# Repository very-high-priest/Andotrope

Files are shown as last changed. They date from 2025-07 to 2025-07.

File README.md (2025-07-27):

# Andotrope
afbeelding



Open Source andotrope I made, for anyone that wants to build their own andotrope.
Credit to the idea of an andotrope goes to Mike Ando https://www.riumplus.com/gehns-holographic-imager-andotrope/
I came up with the method of creating the see through effect.

This is just a prototype and certain things don't work properly yet, please read the issues.

We use a rp2040 zero as the main microcontroller.

Here's a link to the specific screens i bought: 
https://nl.aliexpress.com/item/1005004662221931.html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

Here's the link for the specific battery I bought:
https://www.amazon.com.be/-/nl/Lithium-polymeer-batterij-oplaadbare-connector/dp/B09DPP44C4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

Here's a link for the specific motor I bought:
https://nl.aliexpress.com/item/4001118243931.html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 

Here's a link for the specific magnets I bought:
https://www.digikey.be/nl/products/detail/radial-magnets-inc/8996/5126078

Here's a link for the specific power connector I bought for the motor:
https://www.digikey.be/nl/products/detail/tensility-international-corp/54-00287/16649080 

The powerbrick isn't for sale anymore so you'll have to buy your own 6V barrel connector powerbrick.

Here's the link for the polarised film I used: 
https://nl.aliexpress.com/item/1005006054349865.html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 

Unfortunately the screens themselves are polarised at a 45° angle so you'll have to add another polarisation filter on top if it polarising it horizontally or vertically so the wrap around filter doesn't block the light coming from the filter at the opposite side of the screen holder but only blocks light from the screen itself.

here's the heat inserts I used:
https://nl.aliexpress.com/item/1005003582355741.html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

Here's the screws I used for the heat inserts:
https://nl.aliexpress.com/item/1005005070119421.html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 

I sourced the powerswitch from old christmas lights and soldered it in between the batteries power line. 

The rest of the components you should be able to source from the bill of materials of the scematic.

Here's some more important tips:

Do not solder the mosfet to the bord but rather bridge the source and drain.
I myself glued the screens to the screen holder using double sided tape.
The polarised film has a protective film on both sides that needs to be removed, be carefull because one side of the film is very sticky and should be oriented inwards. This sticky side does help with sticking it to the screens but not to the outside of the screen holder. I used zip ties for that.

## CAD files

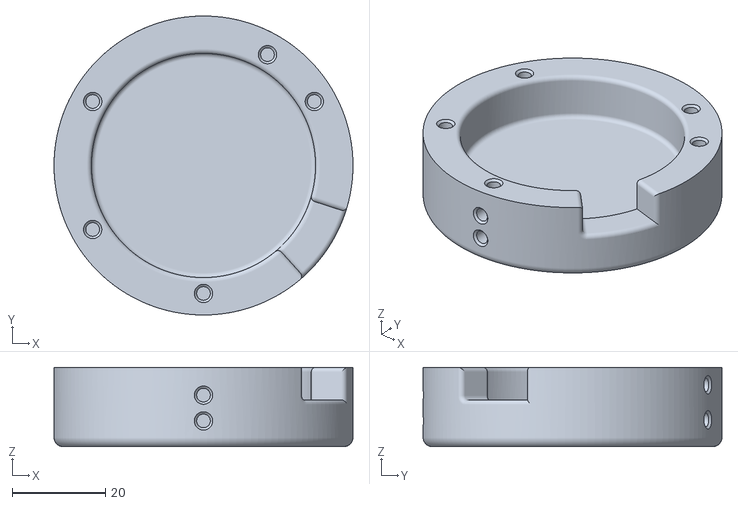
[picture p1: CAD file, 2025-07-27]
3d print files/PCB housing.stl
64.0 x 64.0 x 17.0

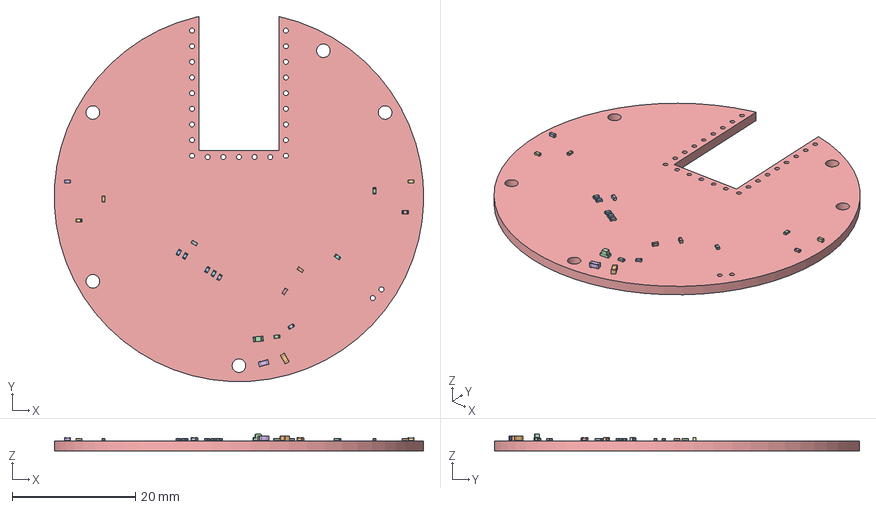
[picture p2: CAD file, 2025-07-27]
FreeCad design files/PCB.FCStd
60.0 x 59.3 x 2.75 mm
C_0402_1005Metric
C_0603_1608Metric
R_0402_1005Metric
LED_0603_1608Metric
R_0402_1005Metric002
C_0603_1608Metric002
C_0402_1005Metric002
R_0402_1005Metric004
R_0402_1005Metric006
R_0402_1005Metric008
R_0402_1005Metric010
R_0402_1005Metric012
C_0402_1005Metric004
C_0402_1005Metric006
R_0402_1005Metric014
R_0402_1005Metric016
R_0402_1005Metric018
C_0402_1005Metric008
R_0402_1005Metric020
R_0402_1005Metric022
abdotrope_PCB

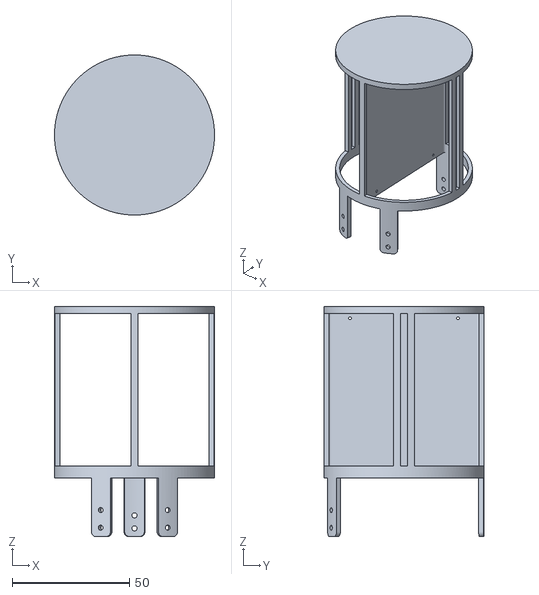
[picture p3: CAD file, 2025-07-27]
3d print files/screen housing.stl
68.2 x 68.2 x 98.0

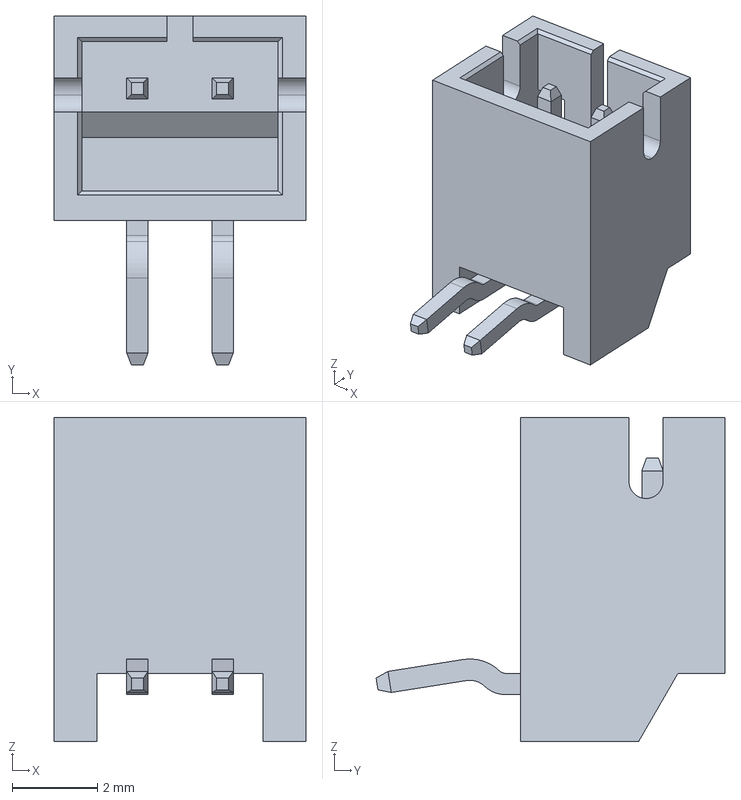
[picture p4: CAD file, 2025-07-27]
FreeCad design files/power connector.FCStd
5.90 x 8.18 x 7.60 mm

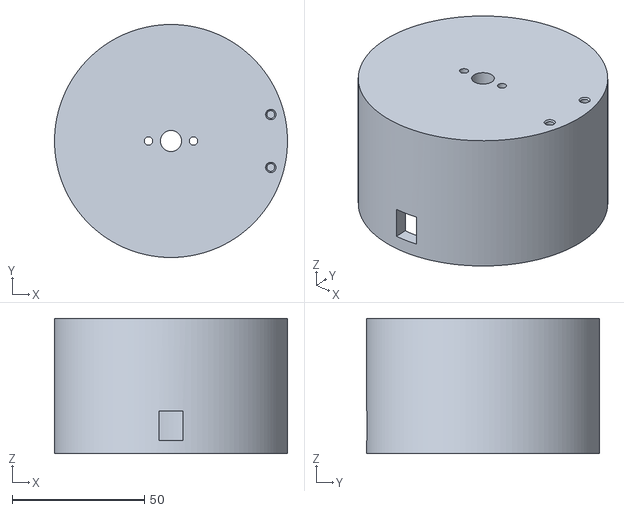
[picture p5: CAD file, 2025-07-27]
3d print files/motor holder.stl
88.0 x 88.0 x 51.0

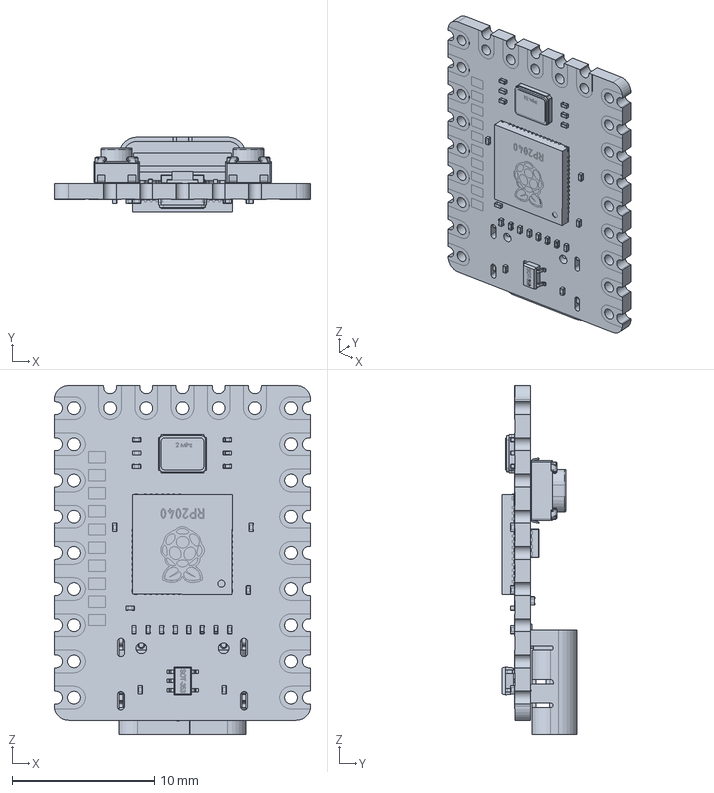
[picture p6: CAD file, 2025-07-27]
FreeCad design files/RP2040-ZERO.FCStd
18.0 x 5.26 x 24.5 mm

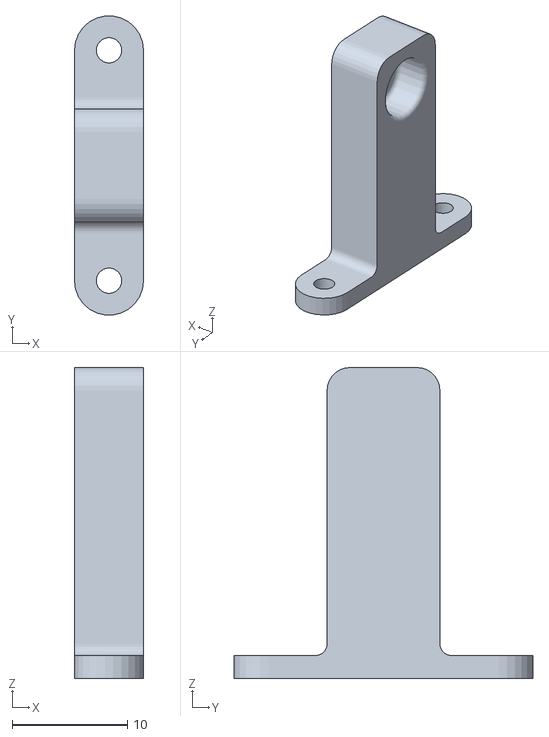
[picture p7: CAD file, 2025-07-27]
3d print files/magnet holder.stl
6.00 x 26.0 x 27.0

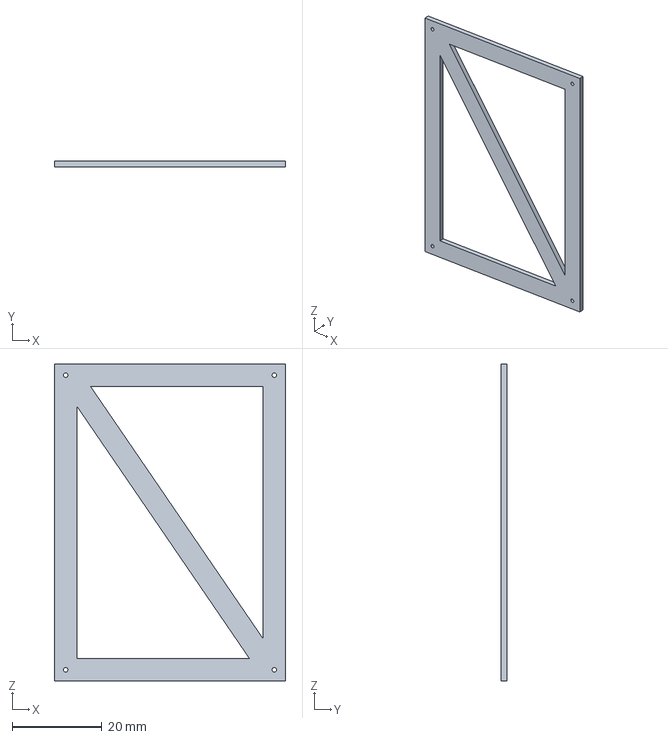
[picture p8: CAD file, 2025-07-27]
FreeCad design files/screen holder.FCStd
51.5 x 1.35 x 70.6 mm

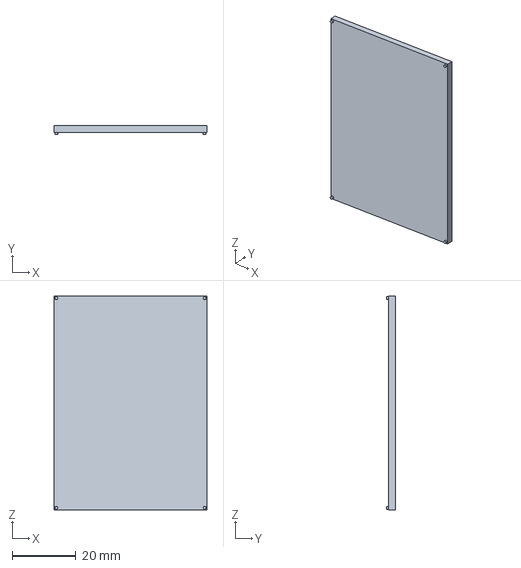
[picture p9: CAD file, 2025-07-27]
FreeCad design files/screen.FCStd
47.8 x 2.78 x 67.0 mm

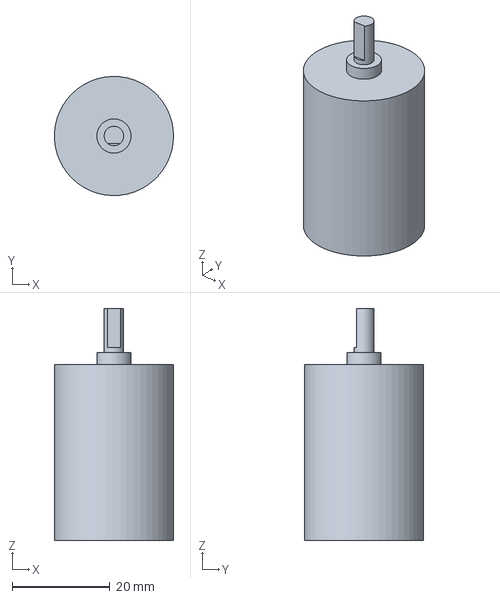
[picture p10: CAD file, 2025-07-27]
FreeCad design files/motor.FCStd
24.4 x 24.4 x 47.5 mm

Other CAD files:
FreeCad design files/spin_assembly.FCStd
FreeCad design files/screen assembly.FCStd
FreeCad design files/andotrope assembly.FCStd
FreeCad design files/blinds.FCStd
FreeCad design files/pcb Housing.FCStd
FreeCad design files/parameter.FCStd
FreeCad design files/motor housing.FCStd

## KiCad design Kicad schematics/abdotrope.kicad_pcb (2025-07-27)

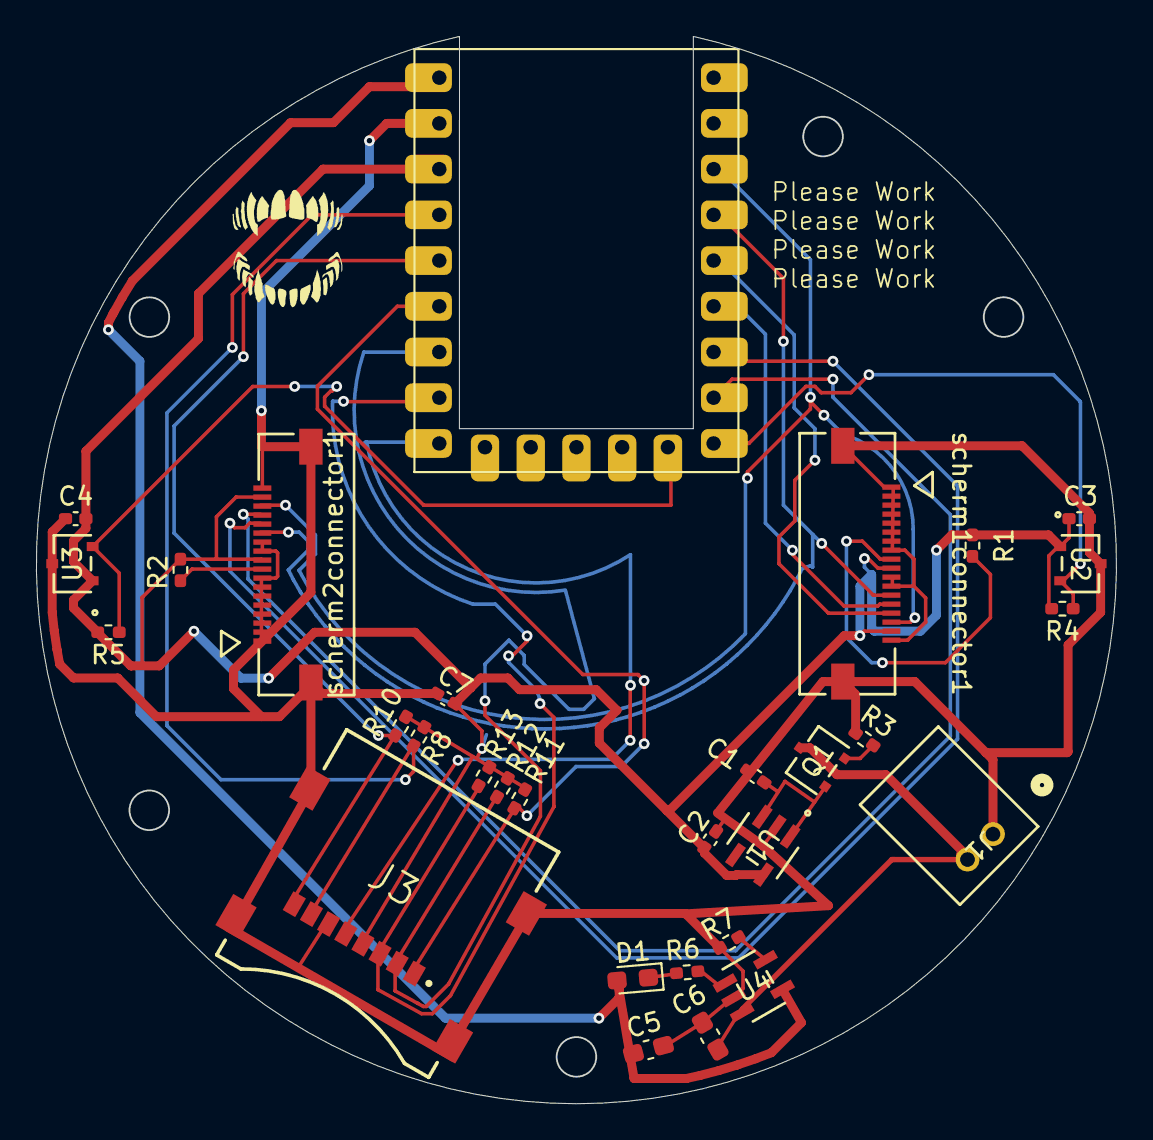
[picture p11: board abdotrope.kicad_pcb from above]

Board: 2 copper layers, 60.0 x 59.3 mm, 30 parts (0 on the bottom side), 25 nets.

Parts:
C1, C2: 1 μF; C_0402_1005Metric_Pad0.74x0.62mm_HandSolder
C3, C4: 0.47 µF; C_0402_1005Metric_Pad0.74x0.62mm_HandSolder
C5, C6: 4,7 μF; C_0603_1608Metric_Pad1.08x0.95mm_HandSolder
C7: 100nF; C_0402_1005Metric_Pad0.74x0.62mm_HandSolder
D1: LED; LED_0603_1608Metric_Pad1.05x0.95mm_HandSolder
J1: S2B-PH-K-SLFSN; CONN_S2B-PH-K-S_JST
J3: MEM2067-02-180-00-A_REVB; GCT_MEM2067-02-180-00-A_REVB
Q1: PMOS (SSM3J372R); SOT-23F_TOS
R1, R2: 10; R_0402_1005Metric_Pad0.72x0.64mm_HandSolder
R3, R8, R10, R11, R12, R13: 10k; R_0402_1005Metric_Pad0.72x0.64mm_HandSolder
R4, R5: 4,7k; R_0402_1005Metric_Pad0.72x0.64mm_HandSolder
R6: 100; R_0402_1005Metric_Pad0.72x0.64mm_HandSolder
R7: 2.8k; R_0402_1005Metric_Pad0.72x0.64mm_HandSolder
RZ1: RP2040-Zero
U1: MIC5504-3.3YM5-TR; SOT-23-5_MC_MCH
U2, U3: TCS40DLR; SOT-23F_TOS
U4: MCP73831T-2ACI/OT; SOT-23-5_MC_MCH
scherm1connector1, scherm2connector1: 5051101892; CON_5051101892_MOL

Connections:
+3.3V: C2.1, C3.2, C4.2, C7.2, J3.4 (VDD), R1.2, R2.2, R4.2, R5.2, R8.1, R10.1, R11.1, R12.1, R13.1, RZ1.21 (3V3), U1.5 (VOUT), U2.1, U3.1, scherm1connector1.10, scherm1connector1.17, scherm2connector1.10, scherm2connector1.17
+5V: C5.1, D1.2 (A), RZ1.23 (GP28), U4.4 (VDD)
GND: C1.2, C2.2, C3.1, C4.1, C5.2, C6.2, C7.1, J1.1, J3.6 (VSS), J3.9 (SHIELD), J3.10 (SHIELD__1), J3.11 (SHIELD__2), J3.12 (SHIELD__3), R3.2, R7.1, RZ1.22 (GP29), U1.2 (GND), U2.3, U3.3, U4.2 (VSS), scherm1connector1.1, scherm1connector1.2, scherm1connector1.3, scherm1connector1.4, scherm1connector1.5, scherm1connector1.6, scherm1connector1.7, scherm1connector1.8, scherm1connector1.11, scherm1connector1.12, scherm1connector1.18, scherm1connector1.P1, scherm1connector1.P2, scherm2connector1.1, scherm2connector1.2, scherm2connector1.3, scherm2connector1.4, scherm2connector1.5, scherm2connector1.6, scherm2connector1.7, scherm2connector1.8, scherm2connector1.11, scherm2connector1.12, scherm2connector1.18, scherm2connector1.P1, scherm2connector1.P2
unnamed: D1.1 (K), R6.1
unnamed: J3.2 (CD/DAT3), R12.2, RZ1.17 (GP26)
unnamed: J3.5 (CLK), RZ1.15 (GP14)
unnamed: J3.3 (CMD), R13.2, RZ1.16 (GP15)
unnamed: J3.7 (DAT0), R8.2, RZ1.20 (GND)
unnamed: J3.8 (DAT1), R10.2, RZ1.19 (5V)
unnamed: J3.1 (DAT2), R11.2, RZ1.18 (GP27)
unnamed: C1.1, Q1.1 (D), U1.1 (VIN), U1.3 (EN)
unnamed: Q1.2 (G), R3.1
unnamed: C6.1, J1.2, Q1.3 (S), U4.3 (VBAT)
unnamed: R1.1, scherm1connector1.9
unnamed: R2.1, scherm2connector1.9
unnamed: RZ1.3 (GP2), scherm1connector1.16, scherm2connector1.16
unnamed: RZ1.4 (GP3), scherm1connector1.13, scherm2connector1.13
unnamed: RZ1.5 (GP4), scherm1connector1.15
unnamed: RZ1.6 (GP5), scherm1connector1.14
unnamed: RZ1.7 (GP6), scherm2connector1.14
unnamed: RZ1.8 (GP7), scherm2connector1.15
unnamed: R4.1, RZ1.9 (GP8), U2.2
unnamed: R5.1, RZ1.10 (GP9), U3.2
unnamed: R7.2, U4.5 (PROG)
unnamed: R6.2, U4.1 (STAT)

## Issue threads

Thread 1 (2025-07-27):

SDIO not supported by RP2040 zero

very-high-priest, 2025-07-27:
The main issue currently that I have is that the SD card is connected through SDIO to the RP2040 zero but there are no libraries for the RP2040 that support SDIO, in C at least.

I did find this work in progress library but that is in rust:
https://github.com/Gip-Gip/rp-sdio

Our current options are either writing a library ourselves, or switching over to an SPI interface. Which could work if we use a seperate spi bus and delegate the 2nd core to getting the images from the sd card and into memory. If that's fast enough for 30fps from the sd card/15fps per second per screen.

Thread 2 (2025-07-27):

rotation assembly bumps into magnet holder. AND magnet is not picked up by hall censors

very-high-priest, 2025-07-27:
While the rotation assembly is rotating it bumbs into the magnet holder through the screws inserted into the screen holder to the pcb holder.

Our options are either to not mind having no magnet holder since precise timing is not super important for our use case or to redesign the magnet holder.

I opt for not putting the magnet holder onto the assembly since it works without.

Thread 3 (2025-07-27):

No power switch/button

very-high-priest, 2025-07-27:
The current PCB doesn't have a power button or switch. The screens are always on even while charging making it go very slowly.
Current fix is to use a power switch to cut the power from the battery and tape it to the side of the rotation assembly.

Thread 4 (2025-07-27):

Very unstable rotation

very-high-priest, 2025-07-27:
While the andotrope is spinning there is more than an noticable wobble. I currently just hold it by the motor itself to show the effect to people. It cannot stand on its own.

This wobble also makes the image displayed less clear.

To fix this issue would require large scale redesigns focused on balancing the rotational assembly and installing some sort of rubber feet on the motor holder.

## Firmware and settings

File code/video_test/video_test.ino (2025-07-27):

#include <Adafruit_GFX.h>
#include <Adafruit_ST7789.h>
#include <SPI.h>
#include <string.h>  // For memset
#include "image.h"

// Display 1 Pins
#define TFT_CS1  5
#define TFT_DC1  4
#define TFT_RST1 -1

// Display 2 Pins
#define TFT_CS2  6
#define TFT_DC2  7
#define TFT_RST2 -1
#define FRAMES 28
#define image_width 183
#define image_height 194

#define screen_width 240
#define screen_height 320

Adafruit_ST7789 tft1(TFT_CS1, TFT_DC1, TFT_RST1);
Adafruit_ST7789 tft2(TFT_CS2, TFT_DC2, TFT_RST2);

// Allocate RAM buffer (150KB)
uint16_t ramImage[screen_width * screen_height]; 

void drawFullscreen(Adafruit_ST7789 &tft) {
  tft.startWrite();
  tft.setAddrWindow(0, 0, screen_width, screen_height);
  tft.writePixels(ramImage, screen_width * screen_height);  // Block transfer
  tft.endWrite();
}

void setup() {
  // Configure SPI
  SPI.setSCK(2);
  SPI.setTX(3);
  SPI.begin();

  // Initialize displays
  tft1.init(screen_width, screen_height, SPI_MODE3);
  tft1.setSPISpeed(62500000);  // 62.5MHz (safe max for ST7789)
  tft1.setRotation(2);
  tft1.invertDisplay(false);  

  tft2.init(screen_width, screen_height, SPI_MODE3);
  tft2.setSPISpeed(62500000);
  tft2.setRotation(2);
  tft2.invertDisplay(false); 
  
  // Draw initial background
  tft1.fillScreen(0x0000);
  tft2.fillScreen(0x0000);
}

void loop() {
  static int i = 0;
  static unsigned long nextFrameTime = 0;

  // Initialize timing on first run
  if (nextFrameTime == 0) {
    nextFrameTime = millis();
  }

  // Wait until scheduled frame time
  unsigned long currentTime = millis();
  if (currentTime < nextFrameTime) {
    delay(nextFrameTime - currentTime);
  }

  // Clear buffer to black (0x0000)
  memset(ramImage, 0, sizeof(ramImage));

  // Calculate centering offsets
  int x_offset = (screen_width - image_width) / 2;  // 28px horizontal margin
  int y_offset = (screen_height - image_height) / 2; // 63px vertical margin

  // Copy image to center of buffer
  uint16_t* dest = ramImage + (y_offset * screen_width) + x_offset;
  const uint16_t* src = epd_bitmap_allArray[i];
  
  for (int row = 0; row < image_height; row++) {
    memcpy_P(dest, src, image_width * sizeof(uint16_t));
    dest += screen_width;  // Move to next display row
    src += image_width;    // Move to next image row
  }

  // Render to both displays
  drawFullscreen(tft1);
  drawFullscreen(tft2);

  // Update frame index
  i = (i + 1) % FRAMES;

  // Schedule next frame (alternate between 66/67ms for 15 FPS average)
  nextFrameTime += 66 + (i % 2);
}

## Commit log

2025-07-27 Main files
    there is a spelling mistake in the kicad files I typed "abdotrope" instead of andotrope
    [PCB housing.stl, PCB.FCStd, RP2040-ZERO.FCStd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]
2025-07-27 shopping list
    shopping list of things you'll need to buy and a couple tips when trying to build one
